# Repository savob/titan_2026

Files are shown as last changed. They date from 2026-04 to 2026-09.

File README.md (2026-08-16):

# TITAN Video System 2026

_One more swing!_

This is the code and hardware that is used to drive the electronics aboard TITAN for the "drive-by-video" system to be hopefully used for the World Human Powered Speed Challenge 2026. **This is heavily based on - and should really be considered a revision of the previous version I made in [2022](https://savobajic.ca/projects/extracurricular/titan-2022/).**

This code is spread across two types of devices, an STM32 microcontroller and Raspberry Pis (RPi) Model 3's. Each rider has an RPi for a total of two units, while there is only one STM32 needed for the vehicle. The STM32 is primarily responsible for collecting vehicle data and passing it to the RPis when requested while the RPis are responsible for displaying the video feed from the RPi Cameras used (hence why each rider needs their own) with an overlay of data collected inside the vehicle. This overlay is tailored to each rider.

There is an additional redundant video system for the front rider based on analog video to minimize potential failure points. This system was entirely off the shelf except for the power regulator, and was entirely disconnected from the remainder of TITAN's electronics to prevent any failure cascade affecting it.

## Folders

The repository is split into folders based on function.

| Folder | Purpose |
| --- | --- |
| `documentation` | Collected MarkDown files detailing various parts of operating TITAN. _NOTE: These are not exhaustive, check the various subsystem `README.md` files for information too!_ |
| `firmware` | Code for the embedded systems, namely the RPi HAT |
| `hardware` | Hardware files for our circuit boards |
| `vision` | Code used to operate the video system on the RPi |

## Hardware

The hardware for TITAN was all designed in [KiCad](https://www.kicad.org/) there are a few boards designed for TITAN with a `readme.md` explaining their purposes. Below is a block diagram of the TITAN system.

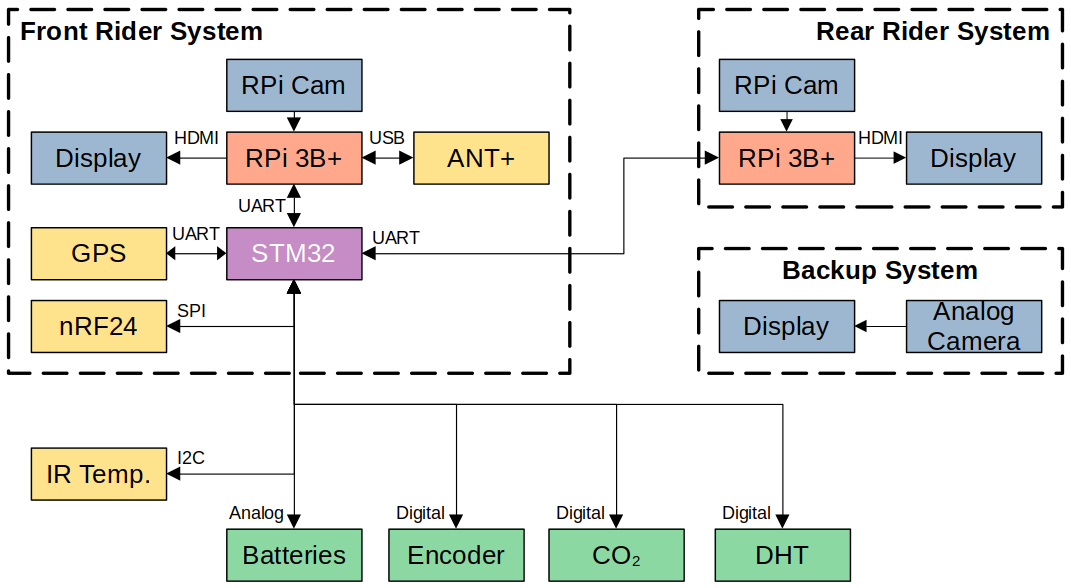
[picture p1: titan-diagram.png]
TITAN Block Diagram


## Microcontroller Code

This is the code prepared for the microcontroller on TITAN. It contains the overall program for TITAN, as well as potentially some other unit tests or variants.

## Raspberry Pi Code

These are responsible for putting video feeds from the outside on the displays for the riders to see from inside. These are overlaid with information collected about TITAN. One of the RPi's has an ANT+ USB module used to collect data from the heart rate monitor and power pedals each rider has and feed it to the STM32 to pass onto the rest of the system.

**The program for running the video feed is run as a separate process to the overlay**, this way if there is a hardware malfunction for the overlay (e.g. the STM32 freezes) then the video feed is uninterrupted for the riders.

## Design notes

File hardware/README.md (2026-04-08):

# TITAN Hardware

These folders contain the projects related to hardware designed to operate TITAN.

They were all designed using KiCad 10.0.

## TITAN Board

The main TITAN hardware is designed to be a HAT (**HA**rdware on **T**op) for the Raspberry Pi 3s we use for video feeds. These HATs perform power regulation for their video systems, data collection, and orchestrate communications between the different systems both inside and outside of TITAN.

## Wheel Board

In TITAN there is small board designed to be located near the wheel brake disks to monitor wheel speed and brake disk temperature for the main board to monitor.

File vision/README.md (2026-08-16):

# Vision Code

This folder is the collection of vision system code running on the RPis. Split between C and Python code.

>[!NOTE]
> Although these files can be viewed and edited off RPis they will only really compile and work properly on RPi 3 microcomputers due to the dependence on some hardware specific libraries, especially for the overlay functionality.

## Setup

>[!IMPORTANT]
> There is a bit of setup needed for this code to work assuming the system is not derived from an image of TITAN in 2022. However I am hazy on the details so this is my best guess.

To setup the ANT receiving system please follow the instruction in [HPVDT's fork](https://github.com/hpvdt/openant) of another fork of OpenAnt.

To configure the C build system for the overlay system one will likely need to execute the following shell commands, although I am unfortunately not certain if they're what I did all those years ago.

```bash
sudo apt install cmake
sudo apt-get install libraspberrypi0
sudo ldconfig -n /opt/vc/lib
```

## Operation

The RPis are configured to boot this system automatically when powered by executing the `titan_startup.py` script when booted (done by editing [rc.local](https://linuxhint.com/use-etc-rc-local-boot/)). To speed this process up, the RPis are configured to boot to command line (CLI) rather than starting the graphical user interface; we believe this also slightly improves the speed of the system.

`titan_startup.py` then launches a series of other processes that collectively represent the TITAN vision system.

- `power_button.py` watches for presses of the 'PWR' button
  - If tapped briefly it merely stops the vision system (useful for development). Entering `startx` into terminal is then needed to start the desktop environment.
  - If held for a few seconds it will shut down the RPi. Presing the button again will start the RPi.
- `camera.py` starts the camera feed and camera recordings

Once these are running, the startup script then responsible for determining whether the RPi is supposed to be the front or rear rider's system based on the presence or absence (respectively) of an ANT+ receiver, and launching the overlay program, `bike.bin`, accordingly by passing it the right arguments.

- If it is the rear system (no ANT+ modules connected), then the startup script just launches `bike.bin` with the arguments needed for the rear system.
- If it is the front system (ANT+ module present), then the startup script launches the `titanant.py` script to read the ANT+ data and pipe it into `bike.bin` to be overlaid and fed to the STM32.

**NOTE: All these scripts/executables are run as separate processes so that if one fails, the others should continue unhindered. Namely the video is never interrupted to the riders.**

## Overlay Code

The overlay code is the main product of this folder, and written in C. It is split up across several function specific C files. Handles communication with the STM32 for data, overlay drawing, and logging as requested.

- `main` - Main file. Reads in arguments provided to determine behaviour (e.g. 'front' or 'rear' system, record logs or not) and then run the main loop to create overlays.
- `antInterface` - Used to process the piped in ANT data from `titanant.py` for use on the overlays and passing on the the STM32
- `overlay` - Responsible for the actually drawing of the overlay. Uses the chipset driver library unique to the RPi 3 hardware to draw the overlay over the video feed. This limits its use to only the 3B or 3B+, and `bike.bin` must be compiled specifically for each model.
- `logging` - Used to write a CSV file of all data collected on the bike
- `racesim` - A C version of our Race Simulation file used to determine how our bike should perform and then compare to how it actually is to see if we're exceeding expectations or not. **UNTESTED**.
- `serialComs` - Responsible for handling communication with the STM32
- `timeTrial` - Used to monitor timing of the code to see how long different sections take to execute. *Used for development purposes, not needed for the riders.*

The code can be edited on the RPi itself, and this is fine for any small tweaks such as some hardcoded constants like wheel radius. However for any larger changes it will likely be easier to offload the editing onto a more capable computer to then copy the changed source code onto an RPi. The exact method to do this is up to you, but I generally opted to move the SD card between the RPi and my laptop.

### Compiling the Overlay Code

If changes are made to any of the Python files, ending in `.py` then one only needs to save and close the files once satisified with the edits made for them to take effect on the next run.

With any changes to the overlay source code in C in the `.c` or `.h` files, one will need to compile a new `bike.bin` for them to take effect.

>[!IMPORTANT]
> Regardless of how the code is edited, it **MUST be compiled on an RPi 3 itself**. This is because overlay code makes use of low level video drivers (VideoCore) for the Broadcom chip that runs the RPi 3 computers, as well as some specific features for some timing code. It is for this reason that many of the `#include` statements and constants will likely be flagged as errors on a non-RPi computer.

The compilation process is based on using a `Makefile` so to generate a new `bike.bin` simply execute the following command in this folder.

```bash
# If changes were only made to .c files
make

# If changes were made to any .h files a clean will ensure they're properly recompiled with .c files
make clean; make
```

The full procedure for this is roughly:

- Replace the contents of the `/home/pi/Desktop/vision` on the RPi SD card with the new file(s)
- Reseat the SD card in the RPi and boot it
- If the video system starts, tap the power button on the RPi HAT to kill the video system and reveal the terminal
- Navigate to the vision folder with `cd /home/pi/Desktop/vision`
- Run `make` in that folder to compile the new binary
- Reboot the system if no errors occur

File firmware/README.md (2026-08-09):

# Microcontroller Code

This folder contains the firmware projects for the embedded system within TITAN going into competition for 2026, targeting the STM32 microcontroller on board. The base for these is the original project from 2022, which was written using the Arduino IDE within the PlatformIO system. Unfortunately I didn't check it before upgrading the microcontroller but the STM32F105 series **lacks any compatibility with the Arduino framework** so a direct port is impossible at present.

This has forced my hand into remaking the project using STM32CubeIDE which is now complete. All code going into the embedded system will be written in C with potentially some C++.

>[!IMPORTANT]
> These firmware projects will generally have "Debug" and "Release" build/upload options. Whenever programming a board to be used in the field **ALWAYS select the "Release" version** as they will be more optimized by the compiler and have some debugging systems (e.g. testing `printf()` lines) stripped out in the pursuit of performance. Only use "Debug" when actively working on a development or performance is not important.

| Project | Purpose |
| --- | --- |
| `titan_2026_rev_a` | Principle firmware to run TITAN boards during races (for both primary and secondary boards) |

## Programming the Boards

To program the STM32 based boards, some version of an STLink is needed to form the connection via a ribbon cable. The [STLINK-V3MINIE](https://www.st.com/en/development-tools/stlink-v3minie.html) is a good tool for this and can be had for a reasonable price. There should be a few of these around the workshop.

>[!TIP]
> The MINIE will not supply power so connect a battery or USB cable to targetted systems. When connecting the ribbon cable to the RPi HAT boards (Rev. A) then the cable is connected such that it covers the LEDs.

If the MINIE is not available there are other more expensive variants or even STM32 development boards also have these built in and can be easily repurposed to program other boards.

>[!NOTE]
> In the past we used bootleg STLink V2 programmers but these will not be recognized and used by STM's software. These also lack consistent pinouts and the protections offered in official offerings.

With the programmer connected to the target board you will then be able to upload firmware using the [STM32CubeIDE](https://www.st.com/en/development-tools/stm32cubeide.html) (compiling from source code) or the [STM32CubeProgrammer](https://www.st.com/en/development-tools/stm32cubeprog.html) (if you have precompiled binaries). For more details on the uploading process refer to ST's own documentation depending on the software used.

## Software Used

All firmware was written using the [STM32CubeIDE](https://www.st.com/en/development-tools/stm32cubeide.html), the projects were configured using [STM32CubeMX](https://www.st.com/en/development-tools/stm32-configurators-and-code-generators.html). These, and most of ST's software is all crossplatform and free to use.

Of these two, STM32CubeIDE is needed to tweak, compile, and then upload firmware. MX is less likely to be needed since that is only used to initally configure the projects and generate code for their hardware, e.g. setting pin functions or configuring communication buses. These configurations don't change significantly except with hardware revisions.

As mentioned earlier the [STM32CubeProgrammer](https://www.st.com/en/development-tools/stm32cubeprog.html) can be used to flash microcontrollers and perform some basic debugging. The problem is that is can only really upload pre-compiled firmware files so you cannot change the firmware using it, for example to adjust wheel diameter.

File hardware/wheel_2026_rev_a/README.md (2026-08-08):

# TITAN Wheel 2026 Rev. A

This board houses a brake temperature sensor as well as a wheel encoder for monitoring speed and distance. It was designed to fit within the wheel bracket close to the brake disk without interfering with the rider's pedaling.

## Changes from 2022

The main changes from the last version will be in improving physical reliability of the system

- Changed everything to other than sensors to be surface mount on the top of the PCB to eliminate the possibility of shorting against mounting surface
- Changed operational amplifier to a TLV2372IDR instead of an LM358 for better performance, namely rail-to-rail output
- Using pads to connect the data cables, headers can be soldered in later if desired
- Removed connector to daisy-chain wheels since that is now handled on the HAT
- Added notes to operate at 3.3&nbsp;V not 5&nbsp;V - although the system can handle it

Looking on data from 2022, there was some noise on the encoder speed signal when plotted alongside the GPS derived speed. This could potentially benefit from filtering the signals, although I would really chalk it up to my firmware not properly capturing each spoke and not using a hardware timer.

## Tuning the Encoder's Comparator Operation

The onboard comparator circuit for the wheel encoder needs to have the two potentiometers to be properly set for reliable operation. One is responsible for the baseline threshold the encoder is compared to to know if the spoke is present of not, labeled `THRES`. The other potentiometer adjusts the level of hysteresis preventing spurious switching by moving the active threshold so the signal can't repeatedly cross it, labeled `HYST`.

To begin, the board must be installed into the wheel bracket and powered, _ideally via the TITAN HAT_. An oscilloscope is strongly recommended to probe the test pads while doing this to complete it accurately but, but not necessary. If possible, perform this with the wheel enclosed in its fairing - or out at least out of direct sunlight as it may influence the IR sensor.

### Without an Oscilloscope

1. Connect the target wheel board to an RPi HAT board and supply power to the HAT board to power the sensor board - battery or USB power is fine.
2. _Gently_ turn both potentiometers entirely counterclockwise to reset them.
3. Rotate the wheel so that the IR sensor is entirely clear of any brake disk spokes.
4. Check that the LED is lit up, if not there may be an issue with the board or too much ambient IR which will need different conditions for testing.
5. Rotate the wheel so a spoke is directly in front of the IR sensor.
6. Turn `THRES` clockwise to increase it until the LED turns off, remember this as the "low" mark.
7. Spin the wheel and make sure that the LED is turning off with each passing of a spoke, and then back on again. Gradually increase `THRES` by turning it clockwise until the LED is no longer turning on again when the spoke is gone - this is the "high" mark.
8. Set `THRES` to be halfway between the "low" and "high" mark. Spinning the wheel should have the LED flash again with each spoke pass.
9. Keep spinning the wheel and increasing `HYST` by turning it clockwise.
10. Once the LED is no longer changing state with the wheel's rotation, this it the "high" mark.
11. Set `HYST` to be about halfway from the starting/zero point to the "high" mark.
12. Spin the wheel to ensure that the LED is flashing again.

This should roughly center the threshold correctly and provide a decent level of hysteresis. _It is impossible for the human eye to perceive the true effect of hysteresis with the LED alone, so we're basically just guessing this._

### With an Oscilloscope

The precise way to do this, no _major_ guesstimations here!

1. Connect the target wheel board to an RPi HAT board and supply power to the HAT board to power the sensor board - battery or USB power is fine.
2. _Gently_ turn both potentiometers entirely counterclockwise to "reset" them.
3. Rotate the wheel so that the IR sensor is entirely clear of any brake disk spokes.
4. Check that the LED is lit up, if not there may be an issue with the board or too much ambient IR which will need different conditions for testing.
5. Read the voltage on the test point labeled `RAW`, this is our ambient level.
6. Rotate the wheel so that there is a spoke directly in front of the IR sensor.
7. Record the voltage on the test point labeled `RAW`, this is our presence level.
8. Gradually turn `THRES` potentiometer until the voltage on the test point labeled `THR` is halfway between the ambient and presence levels. _If the spoke is still in front of the IR sensor at this point, the LED should turn off._
9. Spin the wheel to observe the LED turning on and off as the spoke passes.
10. Keep the wheel spinning and probe `OUT`.
11. Gradually increase `HYST` by turning the potentiometer clockwise until the signal on `OUT` shows a single pulse for each spoke pass rather than a series of pulses during the transition. Then turn `HYST` a sliver more - just not too much so that the `OUT` stops switching
    - If you're also able to probe the other two signals you should be able to see that `THR` is changing between two levels and that `RAW` should be able to cross `THR` only once per spoke passing.
    - `RAW` should continue to a level past `THR` after crossing it, so that even if `THR` didn't move `RAW` would not be causing potential switching with any sensor noise.
    - If the hysteresis gets too large then it might make it hard to catch occasional pulses leading to slower perceived speed.
12. Spin the wheel to ensure that the LED is flashing with each spoke passing.

## Known IR Encoder Issue

There is a fundamental issue with the use of the IR sensor for the wheel encoder: the wheel encoder would fail to track the wheel speed once the brakes were engaged as it gets saturated due to IR radiation from the brake disks reaching temperatures in the multi-hundred degrees as they stop TITAN at the end of runs.

This issue was tolerable as we still had the GPS speed to fallback to, and the brakes would only be engaged when a run was ending so there was no longer a need to know TITAN's exact speed. **Future revisions should consider a different sensor type for the encoder, but this revision kept it since it was field proven and doesn't require modifications to TITAN's wheels.**

A possible hack that could be done using these boards as-is, would be to replace the IR sensor with a visible light discrete LED and photodiode or photoreceptor pair. This should avoid the issue where the brake disk temperature affects the sensor while retaining compatability with the wheels as they are.

A larger overhaul of the board could move to using a magnetic system by attaching magnets to the spokes. If wheel modification is to be avoided, then inductive or capacitive proximity sensing system for the spokes could be considered but the rework needed there would be significant and need collaboration with the mechanical team.

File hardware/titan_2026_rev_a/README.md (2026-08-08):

# TITAN Board

The main custom board for TITAN is designed to be a HAT (**HA**rdware on **T**op) for the Raspberry Pi 3s we use for video feeds. This baseform form factor was inherited from the 2022 version. At the heart of the HAT, there is an STM32 microcontroller which communicates with the RPis and various sensors around TITAN via the various connections present.

## Functionality

These HATs perform four main functions:

1. Regulate power for their RPi and monitor from the battery
2. Facilitate communication between RPis via an STM32 microcontroller
3. Collect data from TITAN using the STM32 microcontroller
4. Handle telemetry broadcast out of TITAN

**Functions 2 to 4 only need to be performed on the "primary" (front rider's) unit.** The secondary (rear rider's) only needs to merely power the RPi and display, and connect to the primary board.

### Power Regulation

These boards receive power directly from LiFePO4 batteries which needs to be regulated down to 5&nbsp;V for the RPi to use, and passed to the display.

The main 3.3&nbsp;V rail for logic will be taken from the RPi for board logic. However there will be an linear regulator and power switch to allow for the USB to power the board safely in the absence of an RPi.

Historically we used 3S packs with a nominal voltage of 9.9&nbsp;V which when really discharged would lead to some screens dimming their backlights, although never fully turning off. So for 2026 I am considering going up to 4S to prevent this happening.

### Sensors

The board hosts several sensors to monitor different things around TITAN. Some sensors are located off board to be better positioned to capture their data such as the wheel sensors. A summary of the sensors interfaced directly with the STM32 in the system is:

- Encoder based wheel speed and distance traveled
- GPS based speed/distance
- Battery levels
- CO2 levels
- Brake temperatures
- Ambient temperature and humidity

### Communication

The STM32 acts a server essentially for data, serving and accepting data from the different system endpoints. Communication with the two RPis is done via UART, and out of TITAN using nRF24 radios.

### Configuration

All boards will be assembled identically, so setting a board for operation in a "primary" or "secondary" role will be needed.

This is partly achieved through hardware design with the `ROLE` signal, but some solder jumpers are needed to portion off the I2C bus on the secondary board to avoid address collisions when connected.

Depending on the displays used there is a solder jumper to provide them with power from either the 5&nbsp;V rail or directly from the battery.

Furthermore there is an additional solder jumper to set the voltage supplied to the wheel sensor system. In 2022 they worked at 5&nbsp;V, but checking the sensors over they should have been supplied 3.3&nbsp;V - so I put the jumper to easily use one or the other.

### Standalone Operation

Although not an critical design constraint, I would like these boards to be able to operate on their own for testing and even use as downlink boards for the crew outside TITAN. So I have incorporated a USB-C connection and some power switches to safely connect to the USB under any configuration of the board.

## Changes from 2022

There are a multitude changes between the 2022 and 2026 versions of the TITAN board, however my desire is to make them all transparent to the system at large (RPis), and minimize the complexity of firmware rewrites for the STM32. In approximate order of implementation:

- Added isolators to be used for inter board UART lines
- Integrated a GPS module
- Integrated environmental sensors
- Using proper wire to board connectors for everything rather than expecting to soldering some wires to the PCB
- Added sensor to monitor battery voltage and current draw per board
- Changed the main microcontroller to an STM32 with more GPIO (STM32F105R)
- Removed reverse polarity input protection for simplicity
- Removed input undervoltage protection, to accommodate varying batteries
- Added on board regulator and power switch ICs to run off USB power if not mounted on an RPi ("standalone")
- Board "role" is determined in hardware based on the connection between the primary and secondary
- Added jumper to select power output to the display connector
- Introduced solder jumper to set wheel power level after finding the sensors used in 2022 were actually rated for 3.3&nbsp;V, _not 5&nbsp;V!_

These cover all the changes I felt were really needed on TITAN. There was only one change that I would like but couldn't justify: integrating the nRF24L01+LNA radio used for telemetry. It would needlessly take me more time to draw the schematic, spec the parts, and then layout while not meaningfully improving any performance metric while greatly increasing the cost compared to just getting a handful of the preassembled modules online. _I'll put aside the vain desire for a majestic monolithic PCB, for now._

## GPS Antenna Network Failure

There is only one critical issue with this board and that's the GPS antenna network routing. This causes the on board GPS module always reports "ANTENNA OPEN" even with an antenna connected or a short to GND. **To work around this issues, an off board module with a separate antenna connection should be soldered in place of the onboard one and use its RX/TX lines.**

Should another revision be made the following steps should be taken to hopefully address this:

- Add via stitching for GPS signal line from antenna to module
- Remove sharp routing bends
- Do not break return path (GND) underneith the GPS signal line
- Move the GPS module more north on the PCB to afford more space for nicer routing
- Choose trace width for a 50&nbsp;Ohm impedance in the final stackup used
- Change components on antenna line to match exactly with known good ones:
  - 6.8&nbsp;nH inductor: Murata LQG15HS6N8J02D
  - 470&nbsp;pH capactior: FH 0402CG471J500NT
  - Connector _(optional, but best to avoid discrepancies)_: BAT Wireless BWU.FL-IPEX1

Below is a figure of the known good reference layout used in another design.

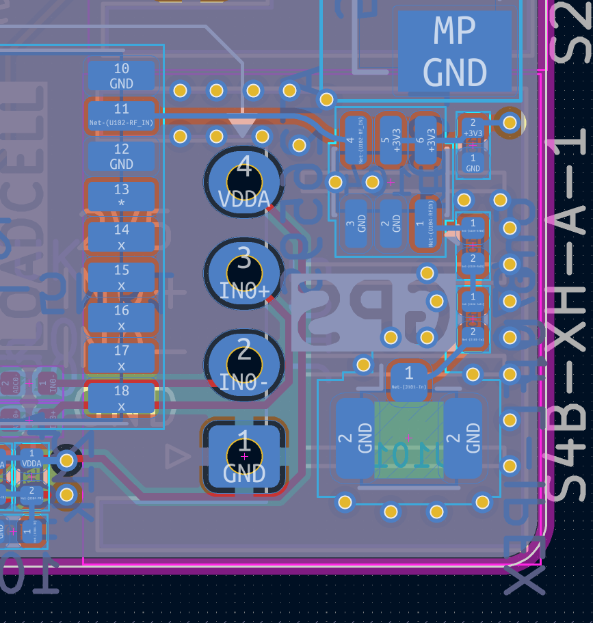
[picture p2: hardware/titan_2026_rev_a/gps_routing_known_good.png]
Known good GPS layout for reference


_This is the first time I've had such issues with radio work so I'm quite dissappointed in this outcome._

## Potential Improvements

These are some minor changes one should consider if a revision or derivative of this work is considered:

- Brake disk temperature sensors work fine at 3.3&nbsp;V so we can remove that solder selection jumper
- Change the serial peripheral facing the secondary system from a UART to a USART so it can make use of DMA receives and transmits
- Add a solder jumper to connect the STM32 to RPi RX so we can ensure that the STM32 secondary board MCU doesn't contest the signal coming from the primary board
- Integrate nRF24 radio circuitry onto PCB
- Change the board so the INA219 is always connected to the STM32 on board, with some knockon changes:
  - No need for the solder jumpers on that I2C line
  - This removes the need for an I2C isolator system, simplifying the isolation requirements
  - The STM32 will always need to be active so the RPi serial line will connect via it to the other board
  - Secondary STM32 will need to poll the INA219 regularly and share that with the primary system

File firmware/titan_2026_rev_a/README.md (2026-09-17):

# TITAN 2026 Code

This is the code meant to operate the entire system. It is meant to be flashed onto bothe boards present in the bike, regardless of position, they will determine their role based on the connections made to them on boot and act appropriately for their role. This firmware was written to provide a transparent replacement for the original 2022 system, so the vision systems can interact with it just like they did with the previous board.

>[!NOTE]
> Although this was meant to facilitate a transparent replacement of the old TITAN electronics system, there are some changes which do slighly break compatibility with the old vision system outlined in the [section on changes](#differences-from-titan-2022).

## Status LEDs

There are three status LEDs located centrally on the board used for various purposes. They are labelled `STATx`, `STAT1` is red while `STAT2` and `STAT3` are white. All these LEDs can be dimmed. Below is a table summarizing various status LED states. If "X" is used then that light doesn't matter to communicate something - for example with non-critical errors. When an LED is "cycling" it is gradually brightening up to a point where it turns off and restarts; the brightness effectively following a sawtooth pattern.

| `STAT1` (Red) | `STAT2` (White) | `STAT3` (White) | Meaning |
| :---: | :---: | :---: | :--- |
| Flashing Quickly | OFF | OFF | **Critical error encountered, microcontroller will reboot momentarily!** _Note: this will not interrupt the video systems._ |
| Cycling dimmly | X | X | **Non-critical issue encountered**, sensor system will continue to fulfil its role in a dimished state. _A sensor might be disconnected._ |
| OFF | X | X | **No issues detected** in by this board as this role. |
| X | OFF | ON | Board is operating as the **secondary board**. |
| X | Cycling | ON | Board is operating as the **primary system, GPS lock in progress.** |
| X | ON | ON | Board is operating as the **primary system, GPS lock completed.** |

## Primary Role (Front Rider)

If determined to be on the primary video system board, the microcontroller will assume the task of operating all real-time tasks for TITAN. Collecting all the data from around the bike's various sensors, processing the data into usable formats, handling communication between the microcomputers running the video systems, and even broadcasting data over radio.

When starting up it will check for all the sensors it expects in the system, should any fail to be identified or configure themselves the microcontroller will ignore them and continue operation. Recovery after boot is not a behaviour yet, so if a sensor is reconnected during operation the system will not notice until rebooted.

>[!IMPORTANT]
> The primary board uses a watchdog timer to ensure it does not get frozen and as a recovery mechanism after a critical error. This means that if the microcontroller freezes or otherwise fails to reset the watchdog timer before it hits zero, the microcontroller will reboot and try to recover with a clean(er) slate. The system has been configured that if such a watchdog reboot occurs then the vehicle data will be preserved into the next boot preventing the loss of distance covered and other measurements. This reboot will not interrupt the video systems in any meaningful way other than a temporary break in data updates.

## Secondary Role (Rear Rider)

When the microcontroller determines it is serving on the secondary system is simply illuminates the status LEDs to indicate this and enters an infinite loop of idling so it doesn't interfere with the operation of the system. No information is collected by or passed through the microcontroller in this role.

## Differences from TITAN 2022

There is **one breaking change** from 2022 which will cause unexpected behaviour on the vision system: instead of reporting the encoder-based (wheel) distance in rotations to the vision system _(which then multiplied it by the wheel circumference itself)_, that distance is now expressed directly as metres to the vision system. This removes the need to maintain the wheel circumference on the vision systems in addition to the microcontroller. The vision code in this repository is compatible with this new method.

Another, minor but not breaking difference is from before is that **we are completely ignoring the DHT11 sensor** as it is very slow to update and requires a long blocking read which would ruin the general responsiveness of TITAN. In its place there is an on board [BME280](https://www.bosch-sensortec.com/en/products/environmental-sensors/humidity-sensors-bme280) sensor to provide the same data in a much faster way, the only downside is that by being mounted on the board it will not be able to accurately measure the outside environment and it'll likely deal with self-heating from the RPi underneath it.

## Potential Improvements

The code as is, can function as a drop in replacement for the 2022 boards (with modified connectors). There are a few minor features or improvemetns that are being considered for future firmware versions:

- [ ] Autodetect the SCD-4x variant used on the board, and add altitude adjustment
- [ ] Add system to adjust the readings from BME280 to approximate the exterior if desired
- [ ] Have the secondary board firmware check if it can find the INA219 IC on the bus to alert users to inproper configuration somehow
- [ ] Make use of the USB connection perhaps for additional debugging interface

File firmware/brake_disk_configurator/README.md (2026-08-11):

# Brake Disk Sensor Configuration Utility

This firmware was made to allow TITAN's brake disk sensors to be configured and tested prior to operation. It is operated using the UART connection via the debug connector, since you'll need that to flash the MCU anyways. Using the debugger will also safely preserve your connection to the system as you potentially power cycle TITAN.

>[!CAUTION]
> Always make connections when the system is unpowered! Please avoid "hot-plugging" the sensors into a powered TITAN board, this may cause damage to the electrical hardware.

## How to Use the Configuration Software

Once you have the firmware flashed to a TITAN 2026 Rev. A board and with the debugger still connected, open a serial terminal on your computer and connect to the debugger's serial port at a **Baudrate of 115200**. Then enter commands as desired, _no need for any newlines or such_. The board processes commands once every couple of seconds so please be patient! All commands follow format `CAA,P` where:

- `C` is the command character
- `AA` is the target senor's I2C address in hexadecimal, e.g. `5A` instead of `90`, _if appicable_
- `P` is an optional parameter _(if not needed for a command the leading comma may be ommited)_

>[!TIP]
> Occaionally only the command character is captured from the user's input, if this happens simply repeat the message until properly received - no harm will come from this. There is no user input that can cause damage to the system.

| Command character | Operation | Address Needed | Parameter |
| :---: | --- | --- | --- |
| `H` | Print help message _(a basic summary of this table)_ | No | None |
| `S` | Scan the bus and report any responsive addresses | No | None |
| `O` | Read object temperature from the sensor | Yes | None |
| `A` | Read ambient (sensor's own) temperature from the sensor | Yes | None |
| `E` | Set object's emissivity as P | Yes | Decimal digits of emissivity (as many digits as desired), e.g. `E5A,769` to set emmisivity of 0.769 at `0x5A`, use 0 to set 1.000 |
| `C` | Change sensor address | Yes | New address in hexadecimal |

>[!NOTE]
> Changes to address and emmissivity properly take effect after the sensor is power cycled.

## General Procedure

If I were doing this I would follow this procedure roughly, the important thing is to ensure that we have sensors at the right addresses above all else so they don't have address collisions inside TITAN since all **sensors are shipped with a default address of 0x5A**. Emmisivity and temperature tests can follow later.

1. With TITAN powered off connect the front brake disk temperature sensor to the bus using the right connector
2. Power up TITAN and run a scan using the appropriate command, only one address should be listed, likely `0x5A`
3. Change this address to the desired address (likely `0x01`, check with a firmware nerd) for the front sensor using the appropriate command
4. Power cycle the system
5. Perform a scan to confirm the address change took effect
6. Power down the board and disconnect the front sensor
7. Repeat steps 1 through 6 with the rear wheel sensor instead, to set it to an address of `0x02` (double check with the firmware nerd)
8. With TITAN powered down connect both sensor
9. Power up the system and conduct a scan and check that both sensors are reporting at their appropriate addresses
10. _(Optional, but recommended)_ Adjust the emissivity of both sensors to match the brake disk material, in 2022 we used `0.600`.

With this done, the rest is really just playing around checking it is reading appropriate temperatures when objects are infront of a given sensor.

>[!IMPORTANT]
> In summary the following parameters should be set before TITAN goes out for a run.
>
> - Front wheel address should be `0x01`
> - Rear wheel address should be `0x02`
> - Both wheels should have an emissivity of `0.600`

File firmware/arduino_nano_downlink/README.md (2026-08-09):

# Arduino Nano Downlink

A simple serial to nRF24 bridge for receiving TITAN braodcasts onto a host PC. Potentially even sending data back to TITAN using acknoledgement packets.

This firmware exists primarily to aid in the development of the radio broadcasts of TITAN by using a known good library. The target hardware is the super old telemetry boards I made to have an nRF24 module backpack on an Arduino Nano, which used the default pinout for the library at the center of this, [RF24](https://github.com/nRF24/RF24).

_The baseline code was taken from the firmware unit tests for TITAN 2022._

## Hardware preparation

This project is prepared for an Arduino Nano with the original bootloader, although it can be easily reconfigured to work for a Nano with the new bootloader or even the classic Uno using the same pinout.

The connections needed to be made are as follow. They are listed in order from pin 1 on the nRF24 (indicated with the square pad) to its neighbour (pin 2) before advancing to the next row.

| Arduino | nRF24 |
| ---: | :--- |
| GND | GND |
| 3.3V | VCC |
| 7 | CE |
| 8 | CSN |
| 13 | SCK |
| 11 | MOSI |
| 12 | MISO |
| 2 | IRQ |

>[!NOTE]
> On the Arduino Nano pin 13 (SCK) is used for the built in LED so it cannot be used in this code, and will flash when there is any SPI activity between the Arduino and radio.

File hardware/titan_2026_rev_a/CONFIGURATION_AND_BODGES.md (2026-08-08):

# Configuring and Fixing TITAN 2026 Rev. A Boards

Before use these board will need the attention of a soldering iron to prepare them for proper operation. It is assumed that you will have access to a soldering iron, a hot air rework station, solder _(preferably lead-free)_, solder flux, solder wick, and tweazers.

## Bill of Materials

The boards weren't fully assembled by the vendor so far, so the following parts are needed to complete the board and complete any fixes. _These numbers are all per board._

- 1 unit - 40-pin (2 rows x 20) 0.1" female pin header, to connect to the RPi.
- 4 sets - 2.5M spacers to hold the HAT to the RPi.
  - Preferably plastic to avoid shorts or damaging the boards.
  - A perfect fit would need 11&nbsp;mm tall spacers but those are rare, so the more common 10&nbsp;mm can be used instead without issue.

These parts are optional, depending on if certain fixes or "upgrades" are desired.

- 1 unit - SCD-41 CO2 sensor. _The SCD-40 can be used too if necessary._
- 1 unit - Replacement UART 3.3&nbsp;V GPS module. The "Ultimate GPS" from 2022 can be used or most other GPS modules readily found online. _Ideally find one with an SMA connector but adaptors exist._
- 1 unit - nRF24L01+LNA module with an SMA connector, to enable telemetry. There should plenty at the workshop, otherwise they're readily available and pretty standardized online.

## Completing the Board

Although the boards were largely assembled by a third party, some pieces were ommitted for various reasons _($$$)_ and need to be hand installed on **ALL** the boards. These parts should be installed in the order below.

1. Solder the 40-pin header for the RPi to the bottom of the board so the HAT may be seated atop the RPi.
2. Proceed to [complete the solder configurations](#configuration-via-solder-jumpers) needed
3. Complete any desired bodges/upgrades listed below
4. Once all soldering is completed to a board, use the spacers to firmly mount the HAT to the RPi before installation into TITAN.

## Configuration via Solder Jumpers

On the TITAN board there are a three clusters of solder jumpers that need to be properly set for the boards to work.

>[!NOTE]
> No damage will occur if any jumper is left open, but it will likely lead to degraded performance since most of these route power or data around the system needed for things to work properly.

### Wheel Power Selection

The first one in the north west, by the power button is for setting the power supply to the wheel boards. **Bridge this one so that `3` is connected to the middle on ALL boards.** This was for development to see if the wheels can reliably operate at 3.3&nbsp;V or if 5&nbsp;V was needed. _If this is incorrectly connected to `5` instead the system will still work, but some damage may happen to the brake temperature sensors with prolonged operation._

### Board Role Selection

Moving toward the microcontroller there are two jumpers that need to be set together to put the board into a primary or secondary role. If the board is meant to function as a primary board connect the pads by `PRIM` to the center, otherwise connect the ones by `SEC`. This will direct to which microcontroller the onboard power monitor connects to so the battery level can be monitored. Connecting the two center pads to different ends will not cause catastrophic failures, however bridging `PRIM` to `SEC` through the middle will cause TITAN systems to fail.

### Monitor Power Selection

The final _mandatory_ bridge is between the two XT-30 connectors. This selects what voltage to apply to the monitor XT-30 between the battery voltage or the onboard regulated 5&nbsp;V rail. Solder this based on the selection of battery and monitor. _I would suggest to use the battery voltage if possible, otherwise the RPi and monitor will fight for the 15&nbsp;W available from the regulator._

### Inter Board Ground Connection

Lastly there is a bridge labelled `GND TIE` near the inter board connectors, **this one can be left open with no drawbacks**. It connects the GND of the two baords together that would otherwise be totally isolated - which enables electrical probing across the two boards, but does slightly undermine some of the protection that the isolation chip offers. _This bridge has no effect on secondary boards._

>[!IMPORTANT]
> Since probing from one board to another is unlikely to ever be needed _(I personally never needed it during my testing of TITAN)_  I strongly recommend that the ground tie (`GND TIE`) be left open for any racing TITAN hardware to offer the maximum protation to failures.

The image below shows a completed TITAN board with the solder jumpers configured for primary operation, with battery power supplied directly to the monitor, and its ground connected to the secondary. _Please ignore the damage to the battery XT-30 from careless soldering!_

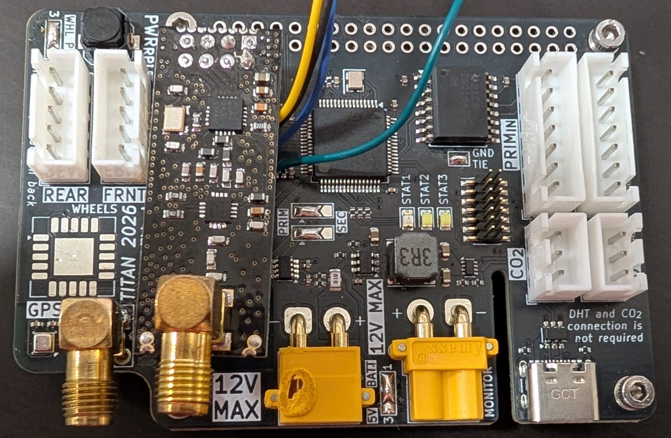
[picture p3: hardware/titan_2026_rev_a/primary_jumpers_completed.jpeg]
TITAN PCB configured for primary operation with the monitor powered directly from the brain


## GPS Issue and Replacement Fix

The only issue the Rev. A board carries is that the GPS antenna circuit doesn't work, rendering the onboard GPS module useless. Leaving the GPS module present will not negatively impact the system, it will simply not provide any useful GPS data to use.

The faulty GPS system can be replaced with a functional off board module with bit of work:

1. Remove the useless GPS module (module with a QR code sticker on top, near the GPS antenna). Be careful to not deform the plastic wheel connectors nearby.
2. Solder wires to the functional pads for the GPS module to connect the offboard module. **`GPS_TX` connects to the TX output of the GPS** module, `GPS_RX` to RX of the GPS.

The connections made to the GPS footprint are shown labelled below.

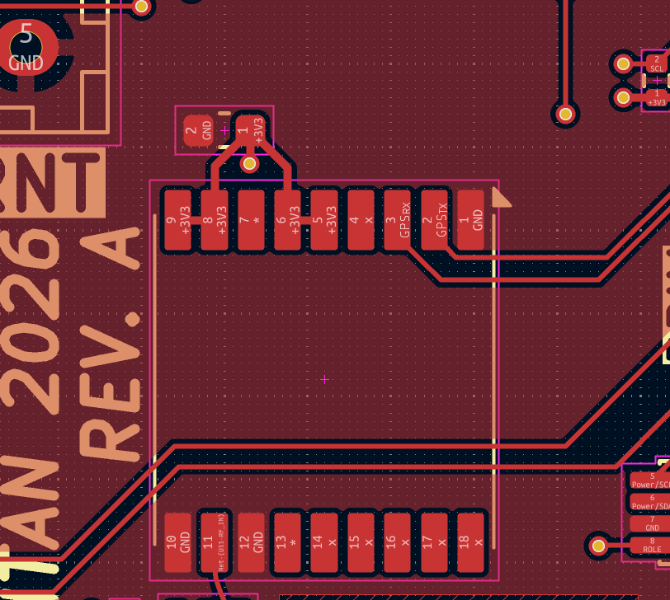
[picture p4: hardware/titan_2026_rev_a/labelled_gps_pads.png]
Labelled pads of the GPS footprint


The image below shows the final result with wires soldered on. Yellow wire for power, black for GPS RX, blue for GPS TX, and green for ground _(don't question the choice of colours!)_

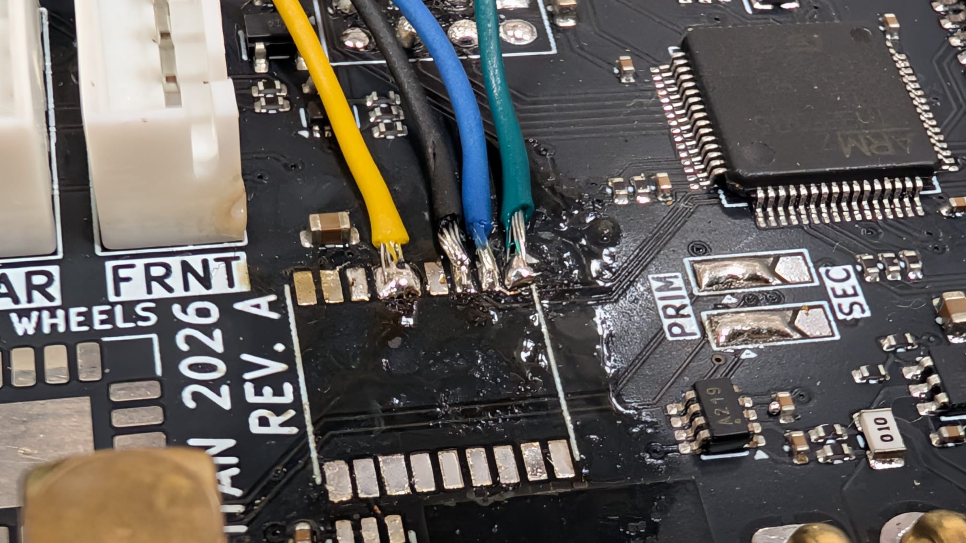
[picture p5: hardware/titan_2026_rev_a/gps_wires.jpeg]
GPS wires connected to vacated pads


## Upgrades, Upgrades

There are some optional things that can be done to improve or make full use of TITAN. TITAN's firmware is designed to check for these and adjust automatically so if these are absent then TITAN will continue to operate without issue.

>[!IMPORTANT]
> These upgrades will only be used if the board is acting as a primary, so there is no need to perform these on boards destined to serve as secondaries.

### SCD-4x CO2 Sensor

This is a low-power digital CO2 sensor that has a footprint allocated on the PCB by the GPS antenna but was ommited from assembly due to its cost and the fact that we already have a decent sensor with the MH-Z19B that covers the same range - albeit power hungry.

The SCD-41 should be used since it has a higher range (400&nbsp;to&nbsp;5000&nbsp;ppm), but the SCD-40 (only 400&nbsp;to&nbsp;2000&nbsp;ppm) is pin compatible in a pinch and the code will retrieve data all the same regardless. The SCD-40 is likely to be overwhelmed during a true run based on previous data showing conditions exceeding 2000&nbsp;ppm quickly into a run.

Placing it on the board is a standard SMT reflow operation. The decoupling capacitor it requires is already populated so only the sensor needs to be placed in the proper orientation.

### nRF24 Radio Installation

Soldering an nRF24L01 module to the empty footprint between the microcontroller and the power button for the RPi will allow the board to broadcast telemetry to a downlink in the chase vehicle or elsewhere. This is a simple through hole soldering operation, simply seat the radio so the antenna connector points the same way as the GPS antenna and solder it down.

>[!CAUTION]
> The nRF24 module will obstruct the GPS module region of the PCB, so do any work on the GPS system prior to installing an nRF24 radio module. This can be seen in the image of the completed solder jumpers.

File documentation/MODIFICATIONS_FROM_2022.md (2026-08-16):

# TITAN Modifications from 2022

There were some hardware changes from 2022 to 2026, these are all principally in the embedded "sensor" system which will need some changes to be made to the TITAN system. For a complete list of changes refer to the `README.md` files for the [main board](../hardware/titan_2026_rev_a/README.md#changes-from-2022) and [wheel board](../hardware/wheel_2026_rev_a/README.md#changes-from-2022) as this will summarize the ones that need to be acted on. These will be sorted into sections based on descending importance to complete.

>[!IMPORTANT]
> This does not cover the modifications and finally assembly needed for the boards themselves, refer to their configuration guides as needed. So far only the main board, the RPi HAT needs [additional hardware work](../hardware/titan_2026_rev_a/CONFIGURATION_AND_BODGES.md) before use.

## Bill of Materials

These are the materials needed to renovate the bike, excluding those to modify/fix anything on the new circuit boards which is covered in their respective guides.

- XT-30 cable connectors, at least 10 of both types
- JST-XH connector kit; with 3-, 5-, and 7-pin connector housings and crimps

## Mandatory Actions

These are actions that must be completed for the new hardware to be usable in TITAN, note that these will make it incompatible with earlier versions as a result.

- **Replace the HAT to HAT cable** this was a 4-pin cable but now will be a 7-pin JST-XH cable.
  - The cable should be a "crossover" cable, so pin 1 on one end goes to pin 7 on the other, and so on.
  - An easy check is if you plug both ends of the cable into the RPi HAT board, the connections should be adjacent to one another. What I mean is that the top connection on `PRIM_IN` should be the same as the top on `SEC_OUT`, and continuing for the length of the connector. If a ribbon cable is used, it should just fold over, but not need twisting to occupy both connectors.
- **Prepare the new 2026 RPi HAT boards** as per their [configuration guide](../hardware/titan_2026_rev_a/CONFIGURATION_AND_BODGES.md) and replace the 2022 HATs
- **Change the battery connectors** from barrel jacks to XT-30F for the RPis
- **Change the monitor power connectors** (to the HATs) from barrel jacks to XT-30M
- **Split the brake/wheel sensor cable harness Y** into a separate one for front and rear wheels
- **Crimp the front and rear wheel sensor cable to use a JST-XH** 5-pin connector abiding by the pinout on the PCB.
  - _Note: not all connections need to be used if not desired. E.g. the front wheel may not use the encoder._
- **Update the power scripts on the RPi** to reflect single button for on and off if using the SD card image from 2022.
  - These are found alongside the vision system code at `/home/pi/Desktop/vision/` on the `rootfs` partition of the SD card

## Optional Changes

These are changes that would be nice and improve TITAN in some way, but are not needed for the system to function.

- **Replace the brake disk sensor board from 2022 with the 2026 version.** The newer boards are almost identical electrically but should present far fewer chances for things to short out and be more reliable in the long run. Soldering the wires to pads can help ensure a low profile cable run preventing damage from riders.
- **Replace the USB-A intermediate wire-to-wire connections with locking connectors** to improve reliability against vibrations. The exact connector doesn't really matter as long as it has a locking feature. _This was a design choice made by me back in 2019 and has carried forth to today, I know much better now!_ If I am not mistaken this is only at the front fork.
- **Replace the four conductor cable used to connect the front wheel sensor with a five conductor one** so the front encoder can be used as well if the wheel board is installed there.
- **Get smaller batteries.** The ones we used in 2022 were 2200&nbsp;mAh or more 3S LiFePO4 if I recall correctly, this is far over sized and needless wight in my opinion. As mentioned in the [operation guide](./OPERATION.md#batteries-and-power), a _fully charged_ 1000&nbsp;mAh 3S LiFePO4 battery is sufficient to run any of the vision systems for around an hour which will suffice for a heat.

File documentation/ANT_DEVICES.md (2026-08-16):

# Working with ANT+ Devices

The ANT+ protocol is used for providing some data from biometric device: the power pedals and heart rate monitors. It's largely being phased out for BLE but we'll stay comfortably in the past.

## Setup

To properly perform the operations needed to use ANT devices you will need some ANT capable receiver and one of their development tools. This can take the form of either:

- ANT USB stick connected to a Windows PC runing [Simulant](https://www.thisisant.com/resources/simulant-1). _You will need to make a free account on their site._
- An Android phone with the [ANT Plugin Sampler App](https://play.google.com/store/apps/details?id=com.dsi.ant.antplus.pluginsampler&hl=en) installed. _This will likely require an old Android phone since many have started dropping ANT support in favour of BLE._

## Recording Expected USB Dongle

The TITAN vision system performs a check on boot to see if an ANT receiver stick is present to determine if it is the primary/front system (ANT present) or not. It does this by checking all the connected USB devices for a vendor and product number (VID/PID) to match what it expects.

>[!IMPORTANT]
> The expected USB dongle must be correctly identified or else no ANT data will be collected for the rider overlays.

This "magic" value it is looking for is recorded in hexadecimal (with lowercase letters) as `ANTStickID` in `titan_startup.py` under `vision/`. An example value is `0fcf:1008` for the currently expected USB stick.

To get the VID/PID of an ANT receiver the [methods differ based on system](https://superuser.com/a/1106248). In either case start by connecting the ANT receiver to your computer.

### Windows USB ID Gathering

Go to "Device manager", find your device, right click on it, select "Properties", go to "Details" tab, select "Hardware IDs" from the drop-down, and you will find an entry of a form:

```terminal
HID\VID_046D&PID_C05A 
```

which are correspondingly vendor and product IDs, i.e. `046d:c05a`

### Linux / RPi USB ID Gathering

Run the following command from your terminal to see pairs of `VID:PID` near the names of all of the USB devices connected.

```bash
lsusb
```

## Pairing Devices

Each ANT device has three device identifying fields that are needed to ensure one connects to the right device. These are the following which are generally 16-bit integers.

- Device number
- Device type
- Transmission type

To acquire this information from a device, one needs to pair with it while using one of the ANT developer tools and record the values reported. These values then need to be copied as appropriate into the `titanant.py` script used under `vision/`.

>[!NOTE]
> There is no need to pair your ANT device to the receiver. Once their identifying information is recorded in the scripts, they will have the ANT receiver search and pair with the devices automatically whenever the system starts.

## Configuring ANT Devices

In TITAN we only use heart rate monitors and torque sensing bicycle pedal ANT devices. Heart rate monitors require no configuration to work properly once paired with a device.

**Torque sensing pedals require a little bit of configuration to properly work**. If I recall correctly, they only need the pedal crank length to be programmed so they properly measure torque and thus power. This can be acheived through the ANT development software mentioned at the start of this file, I personally found using Simulant on PC the easiest.

>[!TIP]
> Once any device is configured it is wise to reboot it and check if the values they report are reasonable through the ANT development tools.

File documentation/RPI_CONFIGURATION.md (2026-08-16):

# Raspberry Pi Configuration

>[!IMPORTANT]
> This is only applicable if starting from scratch with a clean SD card and not using the archived image of TITAN from 2022.

The hardware we use for TITAN are Raspberry Pi Model 3 computers, any subvariant is acceptable (A, B, B+). The system image we have been using for years is for 16&nbsp;GiB microSD cards.

>[!WARNING]
> Much of what was used is now depreciated or obsolete so be careful when updating the images or downloading libraries.

The version of Raspbian _(yes, Raspbian - not Raspberry Pi OS)_ used is "Full" 64-bit version of 11.4 - "Bullseye". Likely the 2022-04-07 release.

The Raspberry Pis were configured years ago with no proper record other than the console log to work with - copied here as `TITAN.bash_history`. From it I've gathered the following pointers on how it was configured.

Check if the VideoCore library and examples are present in the system at `/opt/vc/`. If not try the following remedies:

- Run this in terminal `sudo apt-get install libraspberrypi0`
- Download the `userland` repository at [this commit](https://github.com/raspberrypi/userland/tree/54fd97ae4066a10b6b02089bc769ceed328737e0), the most recent before the 2022 competition, although likely already on the RPi.

With that sorted run the following commands:

```bash
sudo apt install cmake
sudo ldconfig -n /opt/vc/lib
```

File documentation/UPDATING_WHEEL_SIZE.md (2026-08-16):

# Updating Wheel Size

If there are any changes to the _(effective)_ wheel circumference of TITAN they should be reflected properly in the code to ensure we are still calculating speeds and distances correctly from our wheel encoders.

Unfortunately this system inherits a bit of the sloppy design choices I made in 2022 and maybe even as far back as 2019, one such symptom is that we need to update the wheel raduis in multiple places because for some reason I thought it was best to communicate distance in terms of completed rotations rather than a calculated value. If I were to do it again I would only have it set in the microcontroller and provide distance directly.

Luckily the changes are pretty easy to administer in either system. When performing these updates, they should be done for all boards at a time to ensure none are left with the old value - _even the spares!_

## Updating the Microcontroller

The microcontroller has the value hardcoded as `CIRCUMFERENCE_M` in `update_wheel_status()` in `main.c`, simply set it to properly reflect the active circumference in metres.

It may also be necessay to update the number of spokes on the brake disk in this function if the brakedisk is changed.

```c
inline static void update_wheel_status(volatile struct WheelStatus* status, uint32_t capture_period_count) {
    const float CIRCUMFERENCE_M = 2.136;
    const uint8_t SPOKES = 6; // The number of spokes (counts) per complete wheel rotation

    ...
}
```

Once updated you need to program the microcontroller as described in the [firmware `README.md`](../firmware/README.md#programming-the-boards).

## Updating the Video System

In the overlay system the circumference is defined as a global constant `WHEEL_CIRCUMFERENCE_M` at the top of the `main.c` file

```c
const float WHEEL_CIRCUMFERENCE_M = 2.136;
```

Once changed, the overlay code will need to be recompiled into a new binary for the system as described in the [vision system `README.md`](../vision/README.md#compiling-the-overlay-code).

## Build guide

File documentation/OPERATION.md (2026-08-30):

# Operating TITAN

TITAN was designed and tested to be a pretty simple system to operate by requiring no user input beyond a the input to power on, once assembled correctly. This has been preserved with this update to the system, which aimed to not disrupt any of the established TITAN protocols.

>[!NOTE]
> This document assumes the TITAN 2026 electrical system has already assembled and setup. For instructions on how to assemble and setup the TITAN hardware please refer to the [assembly document](./ASSEMBLY.md).

## Batteries and Power

_The system's life force!_ The batteries TITAN was **designed to use 3S LiFePO4 batteries**, so I recommend they continue to be used. Their working range of voltages are 9.0&nbsp;V to 10.8&nbsp;V with a nominal voltage of 9.9&nbsp;V. All batteries should be charged fully prior to any use of TITAN.

Although designed for 3S LiFePO4 batteries, the input of TITAN 2026 can handle a wide range of voltages and still operate without issue. Despite the labeling of `12V MAX`, the RPi board can tolerate between 5&nbsp;V and 17&nbsp;V on the input and provide the needed power for all systems. The stated 12&nbsp;V limit is imposed by the monitor which depending on how the board is configured may draw power from the regulated 5&nbsp;V rail _(in which case the board's own limits still apply)_ or connected directly to the battery which would mean the battery must satisfy the monitor's power requirements. In the the 2022 system the monitors were all designed to handle 12&nbsp;V at most so I kept that warning on the board should the same monitors continue to be used, **please check the monitors used for their power requirements - twice!**

>[!TIP]
> LiFePO4 chemistry batteries are preferred for TITAN due to their safer nature. Their chemistry has a larger range of environmental conditions where it is stable and less dramatic failure modes should the worst come to happen which affords our riders more time to vacate the vehicle in an emergency.

The exact power draw of TITAN is approximately 10&nbsp;W per RPi vision system, about half that for the analog back up system. As such **a 1000&nbsp;mAh 3S LiFePO4 battery can supply a single vision system an hour of operation**. This is plenty for most of our 20 minute heats - but warrants changes for longer testing sessions.

There is circuitry to allow TITAN RPi HATs to seamlessly and safely switch between battery and USB power when in use, should both sources be connected to the board then the battery is selected for power. It is not recommended to use USB power to power an RPi through the HAT as the USB-C connector is configured to only request around 5&nbsp;W of power - enough to run the sensor system.

## Start Up

With TITAN assembled correctly the process to launch the system is pretty straight forward.

> [!CAUTION]
> Failure to follow the battery connection sequence properly may damage the hardware or hinder system operation.

1. Ensure batteries are fully charged
2. Plug in the batteries following this exact order. Each system should automatically begin booting when their battery is connected
   1. Secondary (rear) system
   2. Primary (front) system
   3. Backup system
3. Press the power button (`PWR_RPi`) on RPi systems to boot them if needed - for example if they were shutdown without battery removal

The backup system should show the video feed immediately when turned on. The RPi systems will take about 30 seconds to put the video on screen, which will be preceded with boot messages and a printing of the system's configuration.

## Shut Down

Whenever power is going to be removed from TITAN the following procedure should be followed. Be it at the end of a run, or to conserve battery when staging before a run.

> [!CAUTION]
> Failure to follow this properly may damage the hardware or risk corrupting the data on the RPis.

1. Hold the power button (`PWR_RPi`) on the HAT for a few seconds until it starts shutting down
2. Wait for the video feed to go off and the RPi to shut down properly
   - The video feed should disappear within seconds after the button is pressed, if not press the button again
   - Repeated presses of the off button will not adversely affect the system
   - If the system doesn't shutdown within a minute you may need to connect a keyboard or simply pull the power risking data loss
   - As the RPi shuts down its status LED will flash ten times at 2&nbsp;Hz before going out, that signals it is safe to remove power
3. If desired, disconnect the batteries. They **MUST** be removed in the reverse order they were installed in:
   1. Backup display
   2. Primary system
   3. Secondary system

If the batteries are left in place after the RPis are shutdown, the RPis can be turned on at the press of the power button (`PWR_RPi`). This is useful to do for staging before a run. There is no required order to follow when turning on RPis in this manner because the power supplies have all stabilized.

## Transferring Data To or From the RPis

My _(Savo's)_ preferred method to transfer data was to remove the RPi's micro SD card _(after a proper shutdown with battery removal!)_ and insert it into my computer and directly copy the data of interest onto the computer that way. The only issue is that you'll likely need a Linux machine to recognize the file system the RPis use. Having the SD card in my computer also made it easy to edit some of the scripts to handle things like new power pedals.

Other options include network access or using the RPis as a normal desktop and a USB drive to ferry the data to another computer.

>[!IMPORTANT]
> To get to the desktop of a TITAN RPi one can _quickly_ tap the RPi's power button (`PWR_RPi`) during operation to stop the vision system so the terminal is made visible.

If the button is not working, one can try to manually enter the following sequence of command blindly into the terminal with a keyboard to shut the vision system down. _Best of luck console cowboy!_

```bash
sudo pkill bike
sudo pkill python
```

>[!TIP]
> Entering `startx` in the terminal will start the graphical interface if desired for easier operation of the RPis. _Brace yourself for a slow computer experience._

### Log Files and Locations

By default the TITAN system records data in two locations, one for the videos and another for the ride data.

> [!NOTE]
> All recorded files are timestamped in their names with the start of the run. However the **RPis do not keep time when they are off, so these times will likely lag behind the true start time**. To minimize this time discrepancy the RPis should be allowed to connect to the internet to synchronize their clocks regularly.

| Data | Location | Format |
| --- | --- | --- |
| Ride data | `/home/pi/Desktop/vision/bikelogs/` | `.csv` |
| Video recordings | `/home/pi/Videos` | `.h264` |

### Video Conversion

To convert from `.h264` recordings to the more commonly accepted `.mp4` one may use the following `ffmpeg` command with the appropriate file names substituted for "video":

```bash
ffmpeg -r 60 -i video.h264 -c:v copy video.mp4
```

>[!NOTE]
> The video recordings are known to have portions where the video seems to skip ahead for split seconds. This is likely due to the recording program getting overwhelmed or some hiccup in the `.mp4` conversion process.
>
> Furthermore, the video and overlay/logging are run as separate process so the videos will lack the overlay the rider's had. Also their starting time stamps will likely differ and need a little effort to align if one tries to reconstruct the overlays later.

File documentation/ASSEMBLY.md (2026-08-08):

# Assembly of TITAN 2026

TITAN was once assembled, now it likely is no longer, so someone's got to put it back together. This will be written assuming TITAN's basically being entirely rebuilt.

## Lists of Parts

>[!NOTE]
> These lists do not account for any spare parts, those are up to your discretion.

There are a fair few parts to TITAN needed for operation that need to be packed listed below. Only one unit is needed of each unless specified otherwise.

- 2 x Raspberry Pis Model 3A+ or 3B+
- 2 x 16 GB micro SD cards (larger is fine but the excess storage will not be utilized)
- 2 x approximately 10" 720p HDMI display, 12&nbsp;V supply
- 2 x Raspberry Pi "Spy" camera
- TITAN 2026 HAT assembled for primary operation
- TITAN 2026 HAT assembled for secondary operation
- HDMI cable, 30&nbsp;cm long (for rear rider)
- GPS antenna with SMA connector on 3&nbsp;m cable
- 2.4 GHz antenna with 3&nbsp;m cable
- ANT+ reciever (USB-A)
- Analog pin hole video camera, 12&nbsp;V supply
- 7" analog input display, 12&nbsp;V supply

The following are needed but will likely be already integrated into TITAN's structure, so they don't need to be "packed".

- 3 x Battery extension leads, battery connector to XT-30F, 1.5&nbsp;m long
- 5.5&nbsp;mm barrel jack to barrel jack cable, 3&nbsp;m long
- 5.5&nbsp;mm barrel jack to XT-30F cable, 3&nbsp;m long
- Rear wheel sensor board with harness soldered on
- Brake disk temperature sensor for front wheel with USB-A connector
- USB-A to USB-A cable, 3&nbsp;m long
- HDMI cable, 3&nbsp;m long (for front rider)
- MH-Z19 CO2 sensor with 3&nbsp;m long cable
- 12&nbsp;V power distribution board
- RCA coax video cable, 3&nbsp;m long

## Setup Procedure

>[!CAUTION]
> **All systems must be entirely unpowered for setup!** Remove any and all batteries. The system was not designed for hot-plugging any component so damage may occur as a result.

This starts with the primary digital vision systems for each rider, then the backup system provided to the primary rider.

>[!TIP]
> These steps may be performed in any order when unpowered. Here they are presented in the order that will likely be the most convenient to perform.

1. Check the radio antennas are mounted to the radio window in the tail
   - nRF24 antenna should be positioned normal to the road
   - GPS antenna doesn't need a specific orientation
2. Check the sensors are installed
   - Front wheel brake temperature sensor in wheel bracket
   - Wheel sensor board in the rear wheel's bracket
   - MH-Z19 sensor between the heads of riders
3. Check that the auxiliary sensor connections are made
   - Front wheel sensor intermediate connector is mated near front yoke (might have been disconnected during maintenance or removal of yoke)
   - Front wheel to rear wheel cable harness connection
   - Camera cable extenders are properly securing the ribbon cables if used
   - Antenna cables are routed to electronics area
4. Image the micro SD cards for each RPi and insert them into the RPis
5. Connect the camera cables to each RPi, ensuring they are installed correctly by being perfectly normal to the board
6. Install the RPi HATs, mounted with threaded plastic spacer ideally
7. Insert the ANT+ receiver into the primary/front rider's RPi
8. Connect the sensor to the primary system's HAT paying attention that the sensors are located correctly
9. Connect the radio antennas to the appropriate connectors for the primary board
10. Connect the monitors to the RPis using HDMI cables for video and provide them power from same RPi's HAT
    - In TITAN there should be wires routed from the electronics area to the front rider's viewing area
    - Even the rear rider may require some extension cables to better position the electronics
11. Connect the RPi HATs with the bridge cable, from `SEC_OUT` on the secondary (rear rider's) HAT to `PRIM_IN` on the primary HAT
12. Connect the backup camera to the backup monitor using an RCA cable
13. Connect the backup camera and screen to the 12&nbsp;V power board

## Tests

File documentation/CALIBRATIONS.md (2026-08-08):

# Calibration Protocols

TITAN uses some sensor systems that need calibration to operate at their best, so this document compiles the calibration procedure for those systems.

## Wheel Encoder

On the wheel board there is a circuit which uses an analog IR reflectometer sensor to capture the passing of brake disk spokes. This sensor's analog output is passed through an analog comparator with a hysteresis circuit to be converted into a clean digital signal for the microcontroller to monitor. This section is largely copied from the board's own [`README.md](../hardware/wheel_2026_rev_a/README.md#tuning-the-encoders-comparator-operation).

To calibrate this circuit there are two potentiometers that need to be set: one for the base threshold the sensor's value is compared to, `THRES`, and then a second to increase the amount of hysteresis, `HYST`. Hysteresis is useful in preventing noise on the analog signal to cause multiple switches of the output fooling the system into thinking the wheel is spinning far faster than it is.

This calibration is best performed with the target wheel fully assembled and faired to best reflect the actual operating conditions, as ambient light does affect the sensor. **The only tool needed is a small flat head screwdriver for the potentiometers.** Although this calibration can be performed without any electrical tools, a multimeter or even oscilloscope will help greatly if available.

## Look Ma, No Electrical Tools

Instead of depending on electrical tools, one can complete the calibration with just the status LED present on the board

1. Connect the target wheel board to an RPi HAT board and supply power to the HAT board to power the sensor board - battery or USB power is fine.
2. _Gently_ turn both potentiometers entirely counterclockwise to reset them.
3. Rotate the wheel so that the IR sensor is entirely clear of any brake disk spokes.
4. Check that the LED is lit up, if not there may be an issue with the board or too much ambient IR which will need different conditions for testing.
5. Rotate the wheel so a spoke is directly in front of the IR sensor.
6. Turn `THRES` clockwise to increase it until the LED turns off, remember this as the "low" mark.
7. Spin the wheel and make sure that the LED is turning off with each passing of a spoke, and then back on again. Gradually increase `THRES` by turning it clockwise until the LED is no longer turning on again when the spoke is gone - this is the "high" mark.
8. Set `THRES` to be halfway between the "low" and "high" mark. Spinning the wheel should have the LED flash again with each spoke pass.
9. Keep spinning the wheel and increasing `HYST` by turning it clockwise.
10. Once the LED is no longer changing state with the wheel's rotation, this it the "high" mark.
11. Set `HYST` to be about halfway from the starting/zero point to the "high" mark.
12. Spin the wheel to ensure that the LED is flashing again.

This should roughly center the threshold correctly and provide a decent level of hysteresis. _It is impossible for the human eye to perceive the true effect of hysteresis with the LED alone, so we're basically just guessing this._ After checking with the LED it is nice to start TITAN properly and check that the speed readings shown seem reasonable and do not jump around wildly to accept the calibration.

## The Future is Now Old Man (Electrical Tools)

With some method of monitoring voltage in the system, either with a voltmeter or oscilloscope the process can be performed with more precision by using the solder pads left on the board along the top edge with a ground reference pad for convenience.

The precise way to do this, no _major_ guesstimations here!

1. Connect the target wheel board to an RPi HAT board and supply power to the HAT board to power the sensor board - battery or USB power is fine.
2. _Gently_ turn both potentiometers entirely counterclockwise to "reset" them.
3. Rotate the wheel so that the IR sensor is entirely clear of any brake disk spokes.
4. Check that the LED is lit up, if not there may be an issue with the board or too much ambient IR which will need different conditions for testing.
5. Read the voltage on the test point labeled `RAW`, this is our ambient level.
6. Rotate the wheel so that there is a spoke directly in front of the IR sensor.
7. Record the voltage on the test point labeled `RAW`, this is our presence level.
8. Gradually turn `THRES` potentiometer until the voltage on the test point labeled `THR` is halfway between the ambient and presence levels. _If the spoke is still in front of the IR sensor at this point, the LED should turn off._
9. Spin the wheel to observe the LED turning on and off as the spoke passes.
10. Keep the wheel spinning and probe `OUT`.
11. Gradually increase `HYST` by turning the potentiometer clockwise until the signal on `OUT` shows a single pulse for each spoke pass rather than a series of pulses during the transition. Then turn `HYST` a sliver more - just not too much so that the `OUT` stops switching
    - If you're also able to probe the other two signals you should be able to see that `THR` is changing between two levels and that `RAW` should be able to cross `THR` only once per spoke passing.
    - `RAW` should continue to a level past `THR` after crossing it, so that even if `THR` didn't move `RAW` would not be causing potential switching with any sensor noise.
    - If the hysteresis gets too large then it might make it hard to catch occasional pulses leading to slower perceived speed.
12. Spin the wheel to ensure that the LED is flashing with each spoke passing.

If done correctly with measurements, especially an oscilloscope, then one can be fairly confident in the result of this calibration. Nonetheless, it is still worthwhile to start up TITAN's video system and see the values shown on the overlay match expectations and don't fluctuate wildly.

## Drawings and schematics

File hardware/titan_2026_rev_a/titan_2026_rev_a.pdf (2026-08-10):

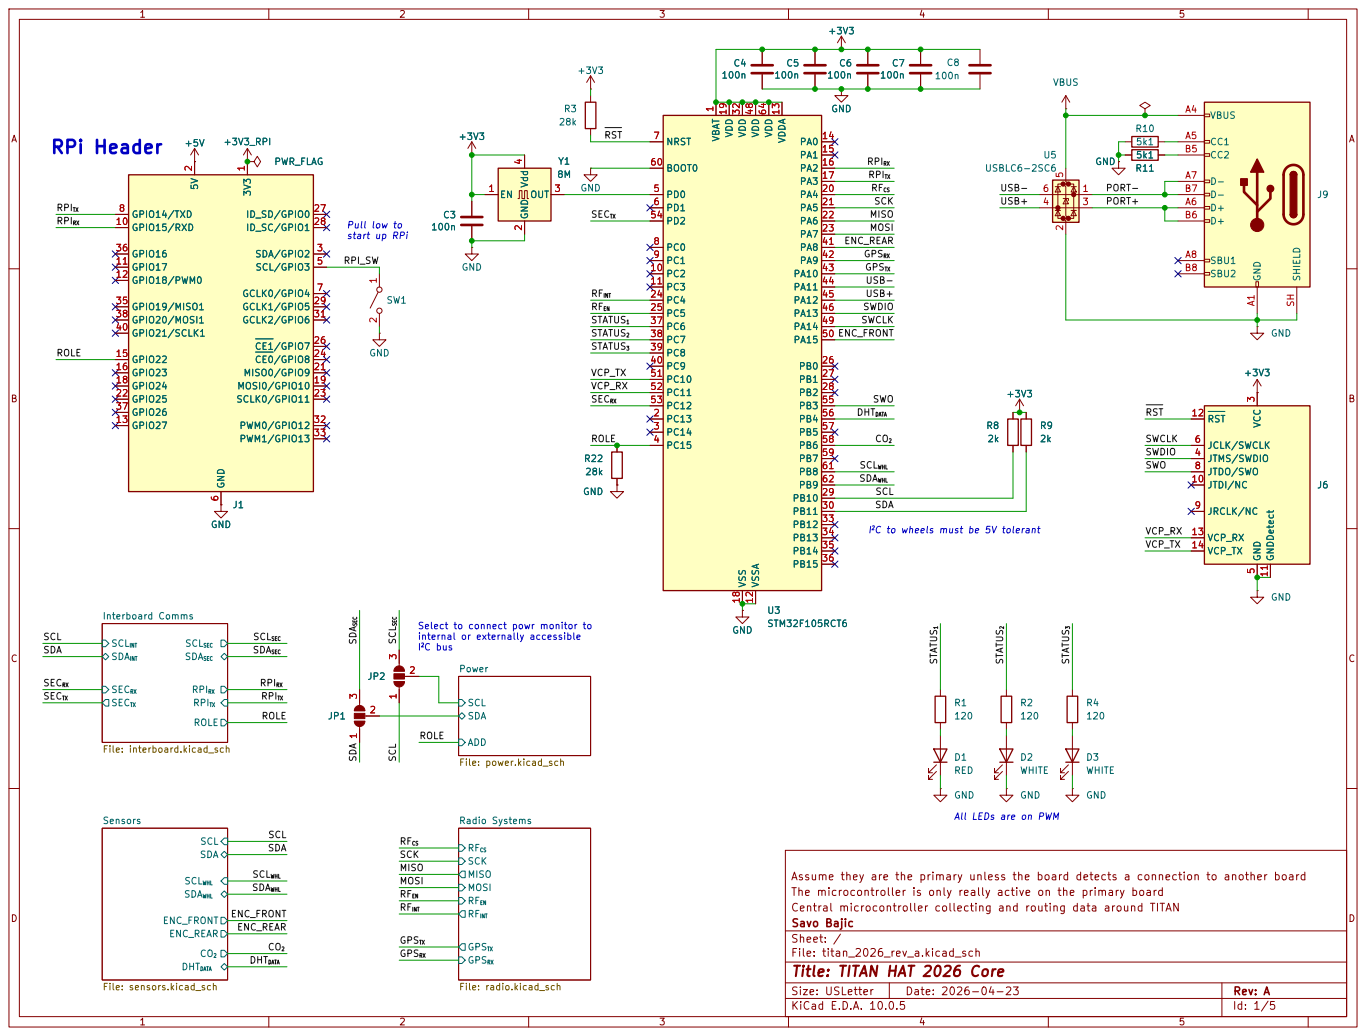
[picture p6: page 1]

I2C to wheels must be 5V tolerant RPi Header

VCP_TX 14 U3
Radio Systems File: radio.kicad_sch SCL SDA

internal or externally accessible

Power File: power.kicad_sch CO2 DHTDATA ENC_FRONT ENC_REAR

SCL SCLWHL SDA SDAWHL Sensors File: sensors.kicad_sch

RFCS RFINT RFEN MOSI MISO

Assume they are the primary unless the board detects a connection to another board
The microcontroller is only really active on the primary board
Central microcontroller collecting and routing data around TITAN
Savo Bajic
Sheet: /
File: titan_2026_rev_a.kicad_sch
Title: TITAN HAT 2026 Core

Size: USLetter | Rev: A
KiCad E.D.A. 10.0.5 | Id: 1/5

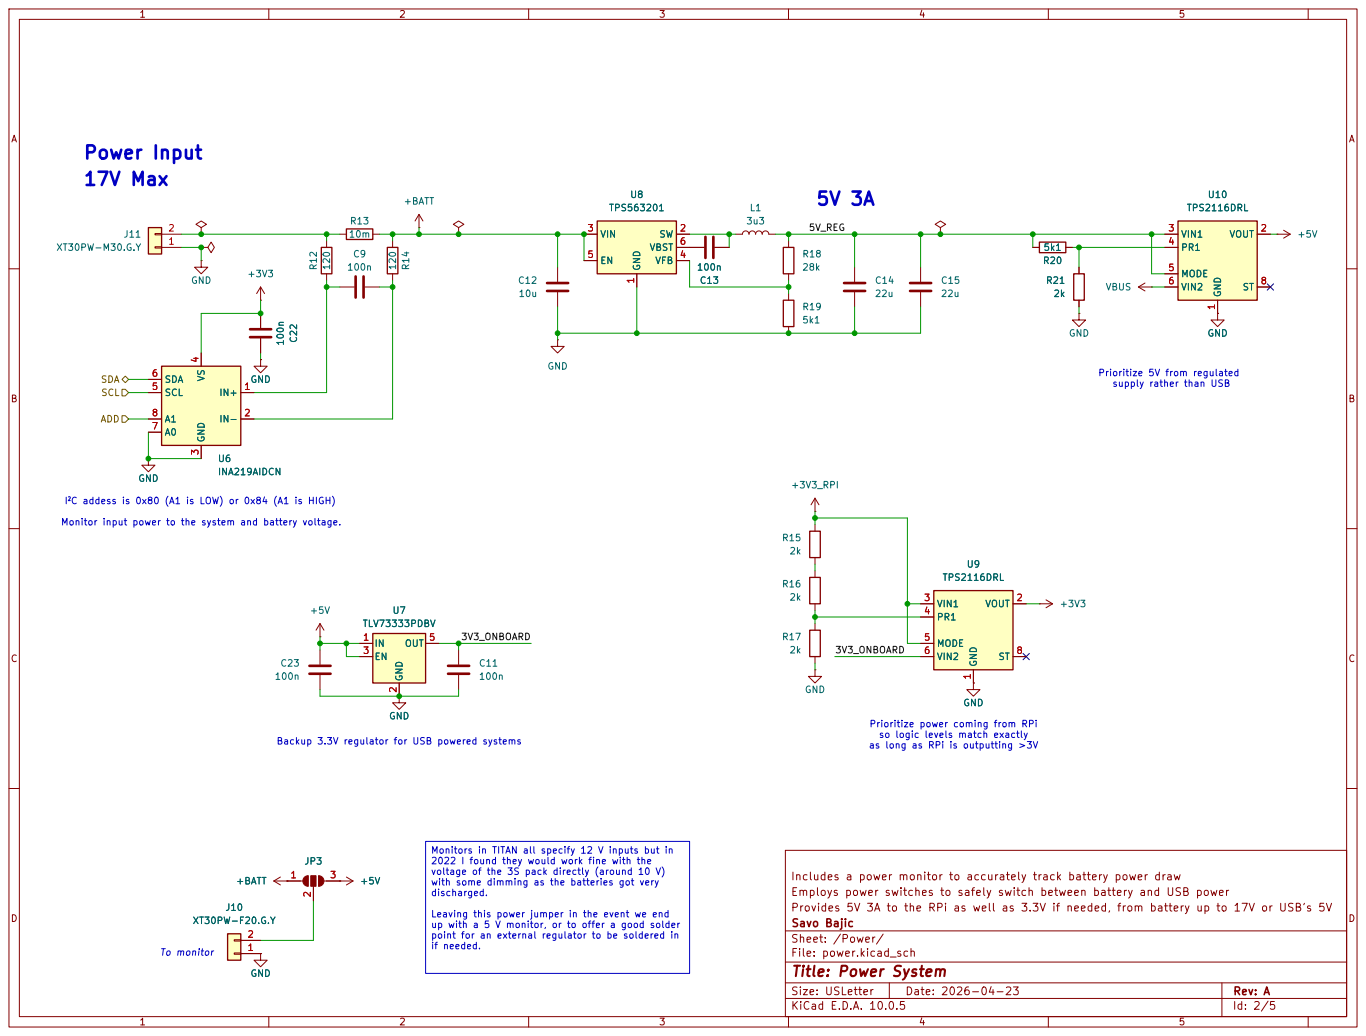
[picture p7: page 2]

Prioritize power coming from RPi so logic levels match exactly as long as RPi is outputting >3V 5V 3A 100n C22 GND U6

supply rather than USB

I2C addess is 0x80 (A1 is LOW) or 0x84 (A1 is HIGH) Monitor input power to the system and battery voltage.

3V3_ONBOARD Monitors in TITAN all specify 12 V inputs but in 2022 I found they would work fine with the

voltage of the 3S pack directly (around 10 V) with some dimming as the batteries got very discharged.

Includes a power monitor to accurately track battery power draw
Employs power switches to safely switch between battery and USB power
Provides 5V 3A to the RPi as well as 3.3V if needed, from battery up to 17V or USB's 5V
Savo Bajic
Sheet: /Power/
File: power.kicad_sch
Title: Power System

Leaving this power jumper in the event we end
up with a 5 V monitor, or to offer a good solder point for an external regulator to be soldered in

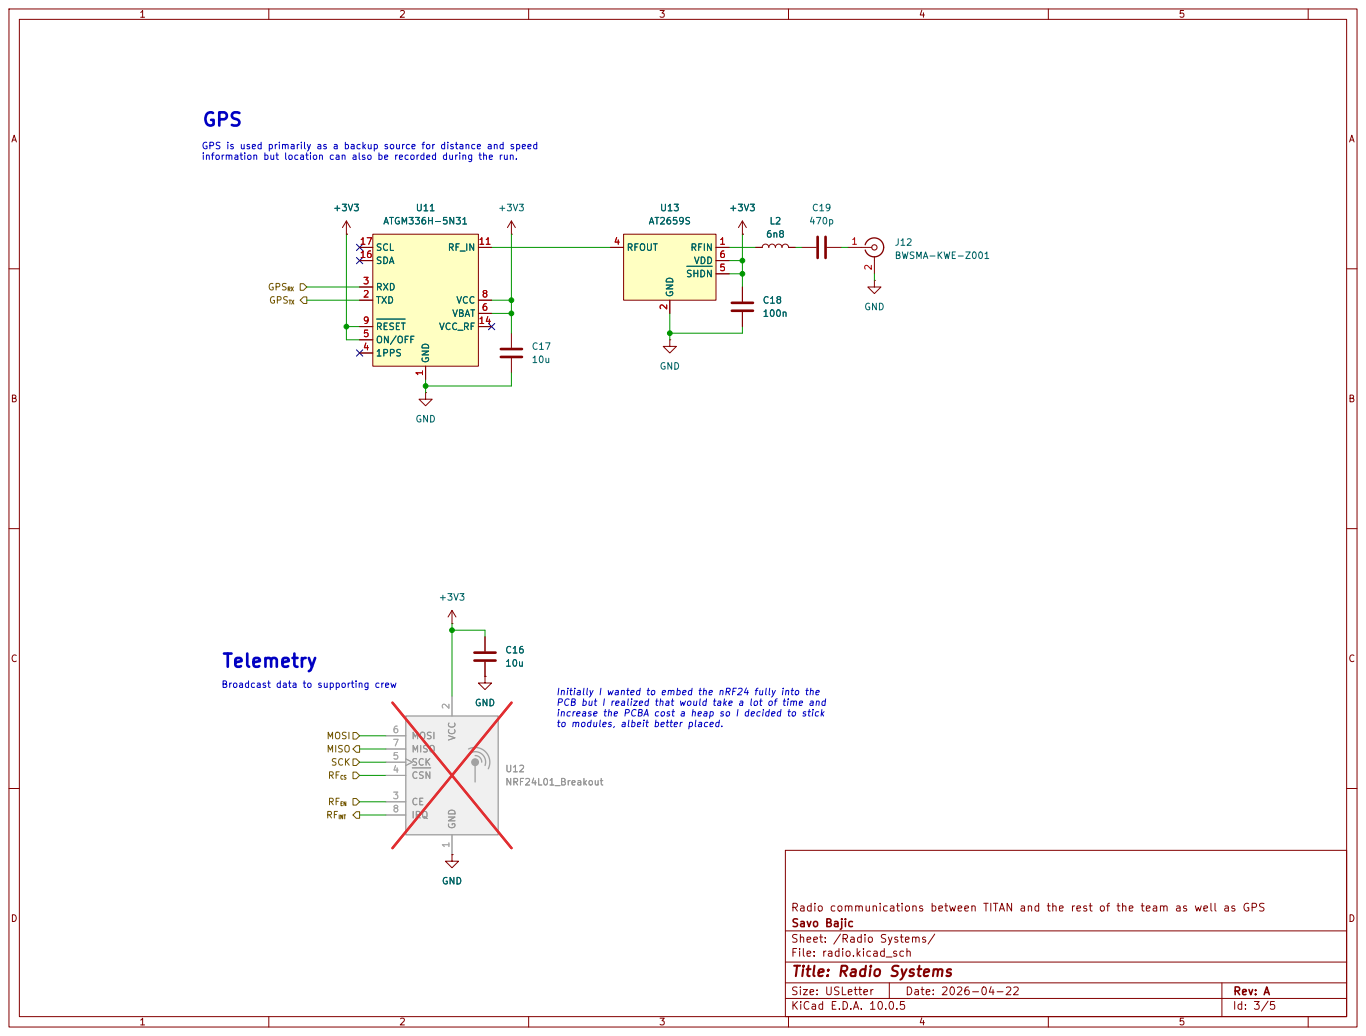
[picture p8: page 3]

information but location can also be recorded during the run. GPS
+3V3 GND
ATGM336H-5N31 GND

GPS is used primarily as a backup source for distance and speed
SDA 16 SCL 17

Broadcast data to supporting crew Telemetry

Initially I wanted to embed the nRF24 fully into the PCB but I realized that would take a lot of time and

increase the PCBA cost a heap so I decided to stick
to modules, albeit better placed.

Radio communications between TITAN and the rest of the team as well as GPS
Savo Bajic
Sheet: /Radio Systems/
File: radio.kicad_sch
Title: Radio Systems

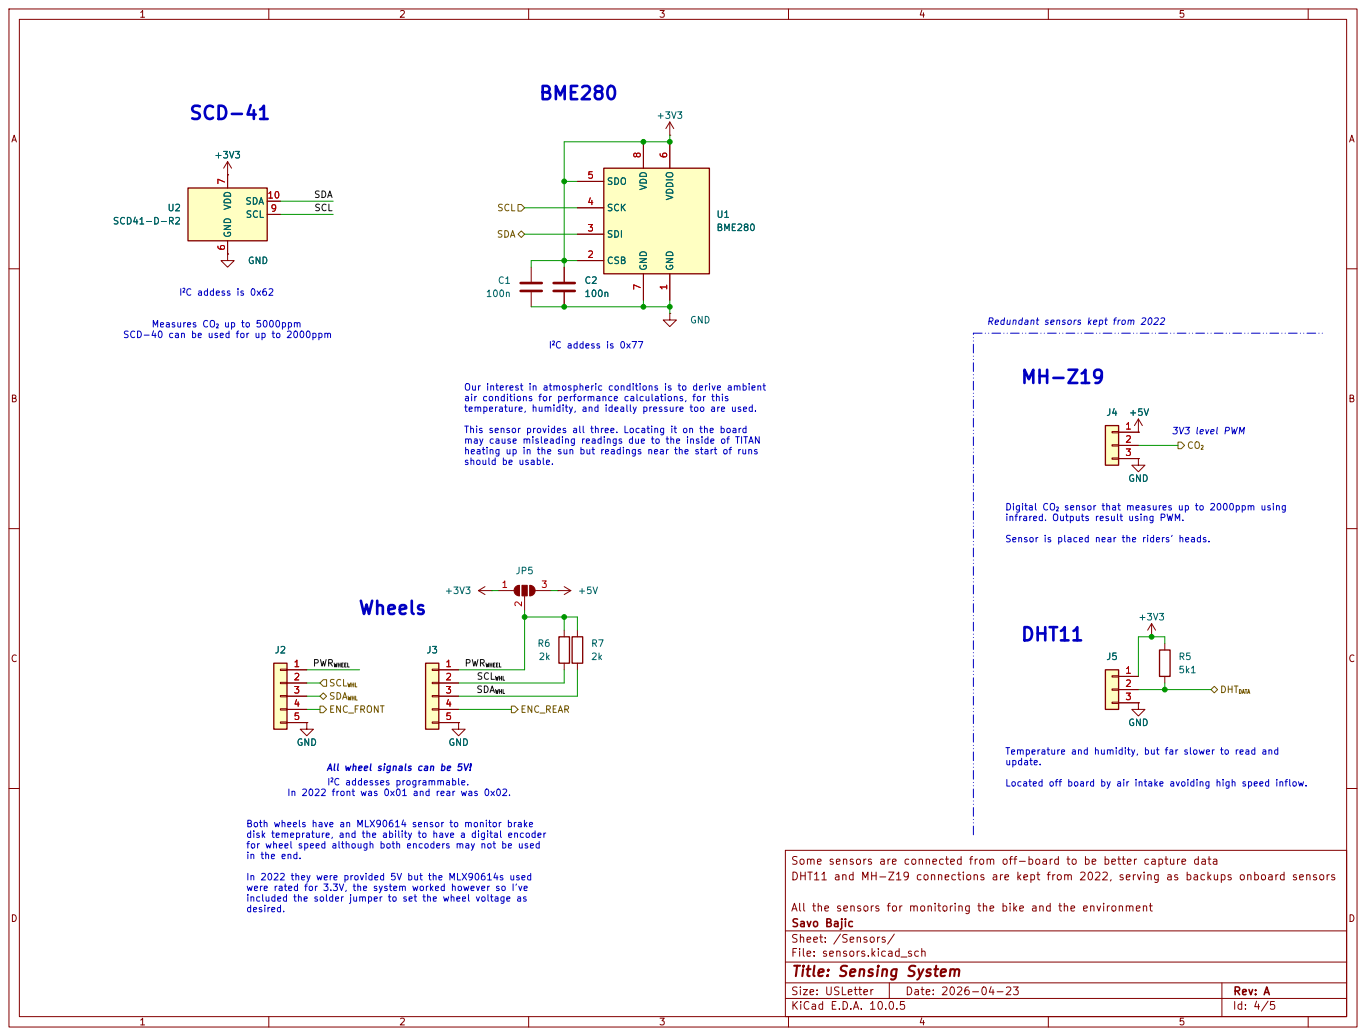
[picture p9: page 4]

Measures CO2 up to 5000ppm
SCD-40 can be used for up to 2000ppm

temperature, humidity, and ideally pressure too are used. This sensor provides all three. Locating it on the board may cause misleading readings due to the inside of TITAN

heating up in the sun but readings near the start of runs

should be usable. Both wheels have an MLX90614 sensor to monitor brake disk temeprature, and the ability to have a digital encoder

update. Located off board by air intake avoiding high speed inflow. Digital CO2 sensor that measures up to 2000ppm using
infrared. Outputs result using PWM. Sensor is placed near the riders' heads.

for wheel speed although both encoders may not be used
in the end.

DHT11 and MH-Z19 connections are kept from 2022, serving as backups onboard sensors Some sensors are connected from off-board to be better capture data

In 2022 they were provided 5V but the MLX90614s used were rated for 3.3V, the system worked however so I've

All the sensors for monitoring the bike and the environment
Savo Bajic
Sheet: /Sensors/
File: sensors.kicad_sch
Title: Sensing System

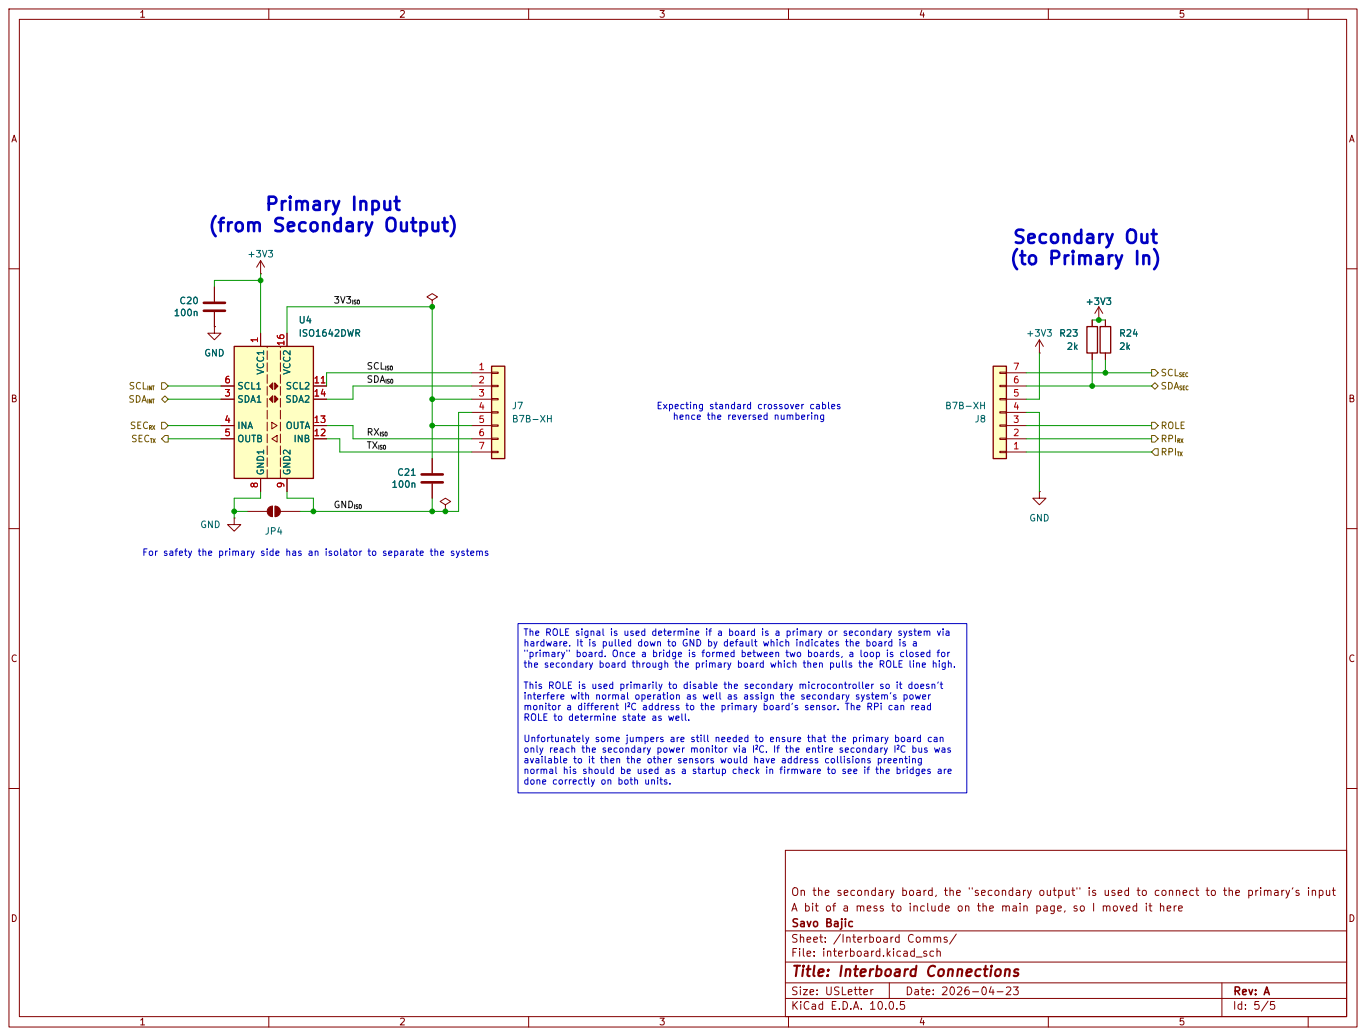
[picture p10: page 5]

normal his should be used as a startup check in firmware to see if the bridges are done correctly on both units. Primary Input (from Secondary Output)

Expecting standard crossover cables hence the reversed numbering

hardware. It is pulled down to GND by default which indicates the board is a
"primary" board. Once a bridge is formed between two boards, a loop is closed for
the secondary board through the primary board which then pulls the ROLE line high. This ROLE is used primarily to disable the secondary microcontroller so it doesn't

interfere with normal operation as well as assign the secondary system's power monitor a different I2C address to the primary board's sensor. The RPi can read ROLE to determine state as well. Unfortunately some jumpers are still needed to ensure that the primary board can

only reach the secondary power monitor via I2C. If the entire secondary I2C bus was available to it then the other sensors would have address collisions preenting
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

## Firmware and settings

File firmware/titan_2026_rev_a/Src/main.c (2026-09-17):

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
/* Includes ------------------------------------------------------------------*/
#include "main.h"
#include "usb_device.h"

/* USER CODE BEGIN Includes */
#include <stdbool.h>
#include "atmosphere.h"
#include "minmea.h"
#include "titan_data.h"
#include "communication.h"
#include "../Drivers/stm32_hal_nrf24_library/NRF24.h"
/* USER CODE END Includes */

I2C_HandleTypeDef hi2c1;
I2C_HandleTypeDef hi2c2;

IWDG_HandleTypeDef hiwdg;

SPI_HandleTypeDef hspi1;

TIM_HandleTypeDef htim1;
TIM_HandleTypeDef htim2;
TIM_HandleTypeDef htim3;
TIM_HandleTypeDef htim4;
TIM_HandleTypeDef htim6;

UART_HandleTypeDef huart4;
UART_HandleTypeDef huart5;
UART_HandleTypeDef huart1;
UART_HandleTypeDef huart2;
DMA_HandleTypeDef hdma_usart1_rx;
DMA_HandleTypeDef hdma_usart2_tx;

/* USER CODE BEGIN PV */
volatile uint16_t mh_z19_co2_ppm = 0;

volatile uint16_t gps_message_length = 0;
volatile uint16_t rpi_message_length = 0;
volatile uint16_t stm_message_length = 0;

const uint32_t I2C_TIMEOUT = 10; // Timeout to be used for I2C interactions

volatile struct TitanSummary summary __attribute__((noinit)); // Preserve data in RAM between boots

// Starting point latitude
const float STARTING_LONGITUDE = -117.043375;
const float STARTING_LATITUDE = 40.393598;

uint8_t rx_addr[5] = {'1', 'N', 'o', 'd', 'e'};
uint8_t tx_addr[5] = {'2', 'N', 'o', 'd', 'e'};

const uint8_t LED_ERROR = 1;
const uint8_t LED_GPS = 2;

const float WHEEL_CIRCUMFERENCE_M = 2.136;
/* USER CODE END PV */

void SystemClock_Config(void);
static void MX_GPIO_Init(void);
static void MX_DMA_Init(void);
static void MX_TIM3_Init(void);
static void MX_I2C1_Init(void);
static void MX_I2C2_Init(void);
static void MX_SPI1_Init(void);
static void MX_TIM4_Init(void);
static void MX_UART4_Init(void);
static void MX_UART5_Init(void);
static void MX_USART1_UART_Init(void);
static void MX_USART2_UART_Init(void);
static void MX_TIM1_Init(void);
static void MX_TIM2_Init(void);
static void MX_IWDG_Init(void);
static void MX_TIM6_Init(void);
/* USER CODE BEGIN PFP */
#ifdef __GNUC__
/* With GCC/RAISONANCE, small printf (option LD Linker->Libraries->Small printf
   set to 'Yes') calls __io_putchar() */
#define PUTCHAR_PROTOTYPE int __io_putchar(int ch)
#else
#define PUTCHAR_PROTOTYPE int fputc(int ch, FILE *f)
#endif /* __GNUC__ */
/* USER CODE END PFP */

/* USER CODE BEGIN 0 */
static HAL_StatusTypeDef led_set_duty(uint8_t led, uint16_t duty) {
	TIM_OC_InitTypeDef sConfigOC = {0};
	sConfigOC.OCMode = TIM_OCMODE_PWM1;
	sConfigOC.Pulse = duty;
	sConfigOC.OCPolarity = TIM_OCPOLARITY_HIGH;
	sConfigOC.OCFastMode = TIM_OCFAST_DISABLE;

	switch (led) {
	case 1:
		return HAL_TIM_PWM_ConfigChannel(&LED_TIMER, &sConfigOC, TIM_CHANNEL_1);
	case 2:
		return HAL_TIM_PWM_ConfigChannel(&LED_TIMER, &sConfigOC, TIM_CHANNEL_2);
	case 3:
		return HAL_TIM_PWM_ConfigChannel(&LED_TIMER, &sConfigOC, TIM_CHANNEL_3);
	default:
		return HAL_ERROR; // Unrecognized LED number
	}

	return HAL_ERROR; // This shouldn't ever be reached
}

static HAL_StatusTypeDef led_sawtooth(uint8_t led) {
	if (led < 1 || led > 3) return HAL_ERROR;

	static uint32_t next_tick[3] = {0, 0, 0};
	static uint32_t current_duty[3] = {0, 0, 0};
	const uint32_t INCREMENT_PERIOD_TICKS[3] = {10, 10, 10};
	const uint16_t MAX_DUTY[3] = {UINT16_MAX / 128, UINT16_MAX, UINT16_MAX};
	const uint16_t DUTY_INCREMENT[3] = {UINT16_MAX / (128 * 500), UINT16_MAX / 200, UINT16_MAX / 200};

	const uint32_t CURRENT_TICK = HAL_GetTick();

	if (CURRENT_TICK < next_tick[led]) return HAL_OK;

	next_tick[led] = CURRENT_TICK + INCREMENT_PERIOD_TICKS[led];

	current_duty[led] = current_duty[led] + DUTY_INCREMENT[led];
	if (current_duty[led] >= MAX_DUTY[led]) current_duty[led] = 0;

	return led_set_duty(led, current_duty[led]);
}
/* USER CODE END 0 */

/**
  * @brief  The application entry point.
  * @retval int
  */
int main(void)
{

  /* USER CODE BEGIN 1 */
	const uint32_t RESET_CODES = RCC->CSR; // Record before they might get cleared
  /* USER CODE END 1 */

  /* MCU Configuration--------------------------------------------------------*/

  /* Reset of all peripherals, Initializes the Flash interface and the Systick. */
  HAL_Init();

  /* Configure the system clock */
  SystemClock_Config();

  /* USER CODE BEGIN SysInit */
  	RCC->CSR = RCC->CSR | RCC_CSR_RMVF; // Clear reset cause for the next run

  	// Check to preserve to ensure data is kept rather than only if it should be cleared since the two may overlap
  	const uint32_t RESETS_TO_PRESERVE_DATA_MASK = RCC_CSR_IWDGRSTF | RCC_CSR_WWDGRSTF | RCC_CSR_SFTRSTF;
  	const bool PRESERVE_DATA = (RESET_CODES & RESETS_TO_PRESERVE_DATA_MASK) != 0;
	if (!PRESERVE_DATA) {
		memset(&summary, 0, sizeof(summary));

    // Non-zero default values
		summary.gps.start_latitude_deg = STARTING_LATITUDE;
		summary.gps.start_longitude_deg = STARTING_LONGITUDE;
	}
  /* USER CODE END SysInit */

  /* Initialize all configured peripherals */
  MX_GPIO_Init();
  MX_DMA_Init();
  MX_TIM3_Init();
  MX_I2C1_Init();
  MX_I2C2_Init();
  MX_SPI1_Init();
  MX_TIM4_Init();
  MX_UART4_Init();
  MX_UART5_Init();
  MX_USART1_UART_Init();
  MX_USART2_UART_Init();
  MX_USB_DEVICE_Init();
  MX_TIM1_Init();
  MX_TIM2_Init();
  MX_IWDG_Init();
  MX_TIM6_Init();
  /* USER CODE BEGIN 2 */
	setbuf(stdin, NULL); //TO HANDLE INPUT BUFFER WHEN USING SCANF/COUT IN C++
	printf("\r\n=========================================\r\n           Starting TITAN 2026\r\n=========================================\r\n");
	if (PRESERVE_DATA) printf("\tData preserved (watchdog reset)\r\n");
	else printf("\tData cleared to defaults\r\n");

	bool non_critical_error = false;
	bool critical_error = false;

	// Start timers once everything's initialized properly
	HAL_TIM_IC_Start_IT(&REAR_ENC_TIMER, TIM_CHANNEL_1);
	HAL_TIM_OC_Start_IT(&REAR_ENC_TIMER, TIM_CHANNEL_2);
	HAL_TIM_IC_Start_IT(&FRONT_ENC_TIMER, TIM_CHANNEL_1);
	HAL_TIM_OC_Start_IT(&FRONT_ENC_TIMER, TIM_CHANNEL_2);
	HAL_TIM_Base_Start_IT(&CO2_TIMER); // Sets up for period elapsed interrupt
	HAL_TIM_IC_Start(&CO2_TIMER, TIM_CHANNEL_1); // Don't care for interrupt on capture here
	HAL_TIM_IC_Start_IT(&CO2_TIMER, TIM_CHANNEL_2);

	HAL_StatusTypeDef ret;
	ret = setup_battery_monitoring(&MAIN_I2C, I2C_TIMEOUT);
	if (ret != HAL_OK) non_critical_error = true;

	ret = atmo_setup(&MAIN_I2C, I2C_TIMEOUT);
	if (ret != HAL_OK) non_critical_error = true;

	ret = setup_brake_disk_sensors(&WHEEL_I2C, I2C_TIMEOUT);
	if (ret != HAL_OK) non_critical_error = true;

	const uint16_t GPS_BUFFER_SIZE = 500;
	char gps_buffer[GPS_BUFFER_SIZE] = {};

	const uint16_t COMMS_BUFFER_SIZE = 64; // Buffer size for data communication buffers
	char rpi_buffer_in[COMMS_BUFFER_SIZE] = {};
	char stm_buffer_in[COMMS_BUFFER_SIZE] = {};
	char rpi_buffer_out[COMMS_BUFFER_SIZE] = {};
	char stm_buffer_out[COMMS_BUFFER_SIZE] = {};

	struct CommunicationInterface primary = { // GPS should never send so don't bother much with it
			.name = "primary",
			.buffer_in = rpi_buffer_in,
			.buffer_in_length = COMMS_BUFFER_SIZE,
			.available_bytes_to_read = &rpi_message_length,
			.buffer_out = rpi_buffer_out,
			.buffer_out_length = COMMS_BUFFER_SIZE,
			.type = INTERFACE_UART_TITAN,
			.prime_read_function = HAL_UARTEx_ReceiveToIdle_IT,
			.send_function = HAL_UART_Transmit_DMA,
			.uart = &PRIM_UART
	};

	struct CommunicationInterface secondary = { // GPS should never send so don't bother much with it
			.name = "secondary",
			.buffer_in = stm_buffer_in,
			.buffer_in_length = COMMS_BUFFER_SIZE,
			.available_bytes_to_read = &stm_message_length,
			.buffer_out = stm_buffer_out,
			.buffer_out_length = COMMS_BUFFER_SIZE,
			.type = INTERFACE_UART_TITAN,
			.prime_read_function = HAL_UARTEx_ReceiveToIdle_IT,
			.send_function = HAL_UART_Transmit_IT,
			.uart = &SEC_UART
	};

	while (GPS_UART.RxState != HAL_UART_STATE_READY) {
		// Wait until ready to receive
	}
	HAL_UART_Receive_DMA(&GPS_UART, (uint8_t*) gps_buffer, GPS_BUFFER_SIZE);

	ret = setup_interface(&primary);
	if (ret != HAL_OK) critical_error = true;
	ret = setup_interface(&secondary);
	if (ret != HAL_OK) critical_error = true;

	struct NRFConfig radio_ext = {
			.hspiX = &RADIO_SPI,
			.spi_w_timeout = 1000,
			.spi_r_timeout = 1000,
			.spi_rw_timeout = 1000,

			.csn_gpio_port = RF_CS_GPIO_Port,
			.csn_gpio_pin = RF_CS_Pin,

			.ce_gpio_port = RF_EN_GPIO_Port,
			.ce_gpio_pin = RF_EN_Pin,
	};

	// Configure radio for dynamic length payloads, although most will be the same length
	ret = nrf24_init(radio_ext, &MICROS_TIMER);
	const bool RADIO_PRESENT = ret == HAL_OK;
	if (RADIO_PRESENT) {
		nrf24_open_tx_pipe(radio_ext, tx_addr);
		nrf24_dpl(radio_ext, enable);
		nrf24_set_rx_dpl(radio_ext, 0, enable);

		nrf24_stop_listen(radio_ext);
		ce_high(radio_ext);
		printf("nRF24 detected and configured to broadcast\n\r");
	}
	else {
		printf("nRF24 not detected, broadcasting will be disabled\n\r");
		// non_critical_error = true; // Radio not installed on any boards used for TITAN so ignore issues
	}

	if (critical_error) {
		Error_Handler();
	}
  /* USER CODE END 2 */

  /* Infinite loop */
  /* USER CODE BEGIN WHILE */
	while (1) {
#ifdef DEBUG
		uint32_t start_loop = MICROS_TIMER.Instance->CNT;
#endif
		HAL_IWDG_Refresh(&hiwdg);

		if (non_critical_error) {
//			led_set_duty(ERROR_LED, UINT16_MAX / 128); // Dim red if systems are diminished but functioning
			led_sawtooth(LED_ERROR); // Cycle error LED slowly
		}
		else led_set_duty(LED_ERROR, 0);
    /* USER CODE END WHILE */

    /* USER CODE BEGIN 3 */
		ret = atmo_conditions_update((struct TitanSummary*) &summary, (uint16_t) mh_z19_co2_ppm);
		ret = read_battery_level((int8_t*)&summary.primary_battery_soc, (int8_t*)&summary.secondary_battery_soc);
		ret = operate_brake_disk_sensors(&summary.front_wheel.brake_disk_temperature_c, &summary.rear_wheel.brake_disk_temperature_c);

		summarize_wheel_data(&summary);

		// Check status of GPS input buffer, takes up to 400 us in Release
#ifdef DEBUG
		uint32_t start = MICROS_TIMER.Instance->CNT;
#endif
		uint_fast16_t current_gps_writing_index = GPS_BUFFER_SIZE - __HAL_DMA_GET_COUNTER(GPS_UART.hdmarx);
		uint_fast16_t last_gps_written_index = (current_gps_writing_index == 0) ? GPS_BUFFER_SIZE - 1 : current_gps_writing_index - 1;
		static uint16_t gps_message_start_index = 0;
		if (gps_buffer[last_gps_written_index] == '\n') {
			bool processed_ok = false;

			if (gps_message_start_index < last_gps_written_index) {
				processed_ok = minmea_process_buffer(&gps_buffer[gps_message_start_index], last_gps_written_index - gps_message_start_index, &summary.gps);
			}
			else {
				// Handle the roll over by copying to a temporary buffer
				char temp_gps[GPS_BUFFER_SIZE];
				uint_fast16_t tail_portion = GPS_BUFFER_SIZE - gps_message_start_index; // In an array of 10 if we start at 6 and need to go to index 2, there are 4 in the tail, 3 in the start
				uint_fast16_t gps_message_length = tail_portion + last_gps_written_index + 1; // +1 to account for zeroth index

				memcpy(temp_gps, &gps_buffer[gps_message_start_index], tail_portion);
				memcpy(&temp_gps[tail_portion], gps_buffer, last_gps_written_index);

				processed_ok = minmea_process_buffer(temp_gps, gps_message_length, &summary.gps);
			}
			// Next message will start after newline
			gps_message_start_index = last_gps_written_index + 1;
			if (gps_message_start_index >= GPS_BUFFER_SIZE) gps_message_start_index = 0;

#ifdef DEBUG
			if (summary.gps.valid_position) {
				uint32_t end = MICROS_TIMER.Instance->CNT;
				uint32_t delta = end - start;
				if (end < start) delta = (end + UINT16_MAX) - start; // Handle rollovers

				printf("GPS processing with a lock took about %lu us\n\r", delta);
			}
#endif
		}
		if (summary.gps.valid_position) {
			led_set_duty(LED_GPS, UINT16_MAX);
		}
		else {
			led_sawtooth(LED_GPS);
		}

		ret = operate_interface(&primary, &summary);
		ret = operate_interface(&secondary, &summary);

		static uint32_t next_broadcast_tick = 0;
		const uint32_t BROADCAST_PERIOD_MS = 500;
		const uint32_t CURRENT_TICK = HAL_GetTick();
		if (CURRENT_TICK > next_broadcast_tick && RADIO_PRESENT) {
			uint8_t trigger_message[] = "{"; // Constantly broadcast summary of TITAN
			uint8_t radio_out[32];
			uint16_t radio_out_length;

			enum MessageStatus status = process_message(&summary, trigger_message, 1, radio_out, sizeof(radio_out)/sizeof(radio_out[0]), &radio_out_length);
			if (status == MESSAGE_PARSED_OK_SEND_RESPONSE) {
				uint8_t radio_err = nrf24_transmit(radio_ext, radio_out, radio_out_length);
#ifdef DEBUG
				switch (radio_err) {
					case 0: // OK
						break;
					case 1:
						printf("Failed radio broadcast: too many retransmissions\r\n");
						break;
					default:
						printf("Failed radio broadcast: %d\r\n", radio_err);
						break;
				}
#endif
			}
			next_broadcast_tick = BROADCAST_PERIOD_MS + CURRENT_TICK;
		}

#ifdef DEBUG
		uint32_t end_loop = MICROS_TIMER.Instance->CNT;
		uint32_t delta_loop = end_loop - start_loop;
		if (end_loop < start_loop) delta_loop = (end_loop + UINT16_MAX) - start_loop; // Handle rollovers

		printf("Loop took about %lu us\n\r", delta_loop);
#endif
	}
  /* USER CODE END 3 */
}

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
/* USER CODE BEGIN 4 */
/**
  * @brief  Retargets the C library printf function to the USART.
  * @param  None
  * @retval None
  */
PUTCHAR_PROTOTYPE
{
  /* Place your implementation of fputc here */
  /* e.g. write a character to the USART1 and Loop until the end of transmission */
  HAL_UART_Transmit(&huart4, (uint8_t *)&ch, 1, 0xFFFF);

  return ch;
}

inline static void update_wheel_status(volatile struct WheelStatus* status, uint32_t capture_period_count) {
	// Using #define to compile hardcoded constant
#define SPOKES 13.0 // The number of spokes (counts) per complete wheel rotation
#define US_PER_COUNT 3.0 // The number of microseconds per clock tick

#define COUNT_TO_KM_P_H (3600000.0 * WHEEL_CIRCUMFERENCE_M / (SPOKES * US_PER_COUNT)) // Divide this by period in count to get speed in km/h

	float speed_km_p_h = COUNT_TO_KM_P_H / (float)(capture_period_count);

	status->speed_kmph = speed_km_p_h;

	status->spoke++;
	if (status->spoke >= SPOKES) {
		status->spoke = 0;
		status->rotations++;
	}

#undef SPOKES
#undef US_PER_COUNT
#undef COUNT_TO_KM_P_H
}

inline static uint16_t calculate_co2_ppm(uint32_t duty_count, uint32_t period_count) {
	// Duty should always be smaller than the full period
	if (duty_count > period_count) {
		return -1;
	}
	const float duty = (float)duty_count;
	const float period = (float)period_count;

	// To deal with the 5% tolerance on timing the measurements are all derived from portions

	const float END_PORTION = 2.0 / 1004.0; // The portion of constant dead time for high and low portions
	const float END_TIME = period * END_PORTION;
	const float HIGH_TIME = duty - END_TIME;

	// Check if the pulse captured was too small and mistaken for negative
	if (HIGH_TIME < 0) {
		return -1;
	}

	const float DATA_PERIOD = period * (1 - (2 * END_PORTION)); // Discount the high and low dead time
	const float PORTION = HIGH_TIME / DATA_PERIOD; // The actual data duty/portion discounting the holds at each level

	const float PPM_RANGE = 5000.0; // Range of measurement for the CO2 sensor installed
	return (uint16_t)(PORTION * PPM_RANGE);
}

void HAL_TIM_IC_CaptureCallback (TIM_HandleTypeDef * htim) {
	uint32_t captured_value = HAL_TIM_ReadCapturedValue(htim, TIM_CHANNEL_1); // All our captures need channel 1 value

	/* For wheel speeds we want to ignore the first capture after an overflow since
	 * it will not properly represent speed since we won't know how many timeouts
	 * have elapsed and accidentally give a false high speed
	 *
	 * To that end if speed is 0 we do one update to a miniscule speed so the next
	 * update recognizes a non-zero value.
	 *
	 * We won't bother with a spoke count update on the first post timeout edge
	 * as it might very well be a reversed rotation. Realistically in normal
	 * operation when we care for distance we won't be going slow enough for this
	 * to matter.
	 */

	if (htim->Instance == REAR_ENC_TIMER.Instance) {
		if (summary.rear_wheel.speed_kmph != 0) update_wheel_status(&summary.rear_wheel, captured_value);
		else {
			summary.rear_wheel.speed_kmph = 0.1;
		}
		return;
	}
	if (htim->Instance == FRONT_ENC_TIMER.Instance) {
		if (summary.front_wheel.speed_kmph != 0) update_wheel_status(&summary.front_wheel, captured_value);
		else {
			summary.front_wheel.speed_kmph = 0.1;
		}
		return;
	}

	if (htim->Instance == CO2_TIMER.Instance) {
		// CO2 calculation
		uint32_t duty_period = HAL_TIM_ReadCapturedValue(htim, TIM_CHANNEL_2);
		mh_z19_co2_ppm = calculate_co2_ppm(duty_period, captured_value);
		return;
	}
}

void HAL_TIM_PeriodElapsedCallback (TIM_HandleTypeDef * htim) {
	if (htim->Instance == CO2_TIMER.Instance) {
		mh_z19_co2_ppm = 0;
		return;
	}
}

void HAL_TIM_OC_DelayElapsedCallback (TIM_HandleTypeDef * htim) {
	// On a timeout we've probably stopped
	if (htim->Instance == REAR_ENC_TIMER.Instance) {
		summary.rear_wheel.speed_kmph = 0;
		return;
	}
	if (htim->Instance == FRONT_ENC_TIMER.Instance) {
		summary.front_wheel.speed_kmph = 0;
		return;
	}
}

void HAL_UARTEx_RxEventCallback(UART_HandleTypeDef *huart, uint16_t Size) {
	if (huart == &GPS_UART) gps_message_length = Size;
	if (huart == &PRIM_UART) rpi_message_length = Size;
	if (huart == &SEC_UART) stm_message_length = Size;
	// Leave the trigger for the next DMA until after the buffer parsed or copied elsewhere to prevent the current message being lost
}

void HAL_UART_ErrorCallback(UART_HandleTypeDef *huart) {
	HAL_IWDG_Refresh(&hiwdg); // Allow the lights to flash for a bit before we recover

	uint32_t error_code = huart->ErrorCode;

	if (error_code == HAL_UART_ERROR_ORE) {
		// As per 27.6.1 in reference manual we can clear this error flag by reading SR and then DR
		(void) huart->Instance->SR;
		(void) huart->Instance->DR;
		if (huart->ErrorCode == HAL_UART_ERROR_ORE) {
			if (huart == &GPS_UART) printf("Error OVERRUN on GPS line PERSISTS\r\n");
			if (huart == &PRIM_UART) printf("Error OVERRUN on primary line PERSISTS\r\n");
			if (huart == &SEC_UART) printf("Error OVERRUN on secondary line PERSISTS\r\n");
		}
		else {
			if (huart == &GPS_UART) printf("Error OVERRUN on GPS line CLEARED. Comms may need a few transactions to recover fully.\r\n");
			if (huart == &PRIM_UART) printf("Error OVERRUN on primary line CLEARED. Comms may need a few transactions to recover fully.\r\n");
			if (huart == &SEC_UART) printf("Error OVERRUN on secondary line CLEARED. Comms may need a few transactions to recover fully.\r\n");
			return;
		}
	}
	else {
		if (huart == &GPS_UART) printf("Error %ld on GPS line\r\n", error_code);
		if (huart == &PRIM_UART) printf("Error %ld on primary line\r\n", error_code);
		if (huart == &SEC_UART) printf("Error %ld on secondary line\r\n", error_code);
	}

	Error_Handler();
}
/* USER CODE END 4 */
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


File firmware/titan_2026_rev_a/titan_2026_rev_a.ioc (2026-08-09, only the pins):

Mcu.UserName=STM32F105RCTx
PA10.GPIO_Label=GPS_TX
PA10.Signal=USART1_RX
PA11.Signal=USB_OTG_FS_DM
PA12.Signal=USB_OTG_FS_DP
PA13.Signal=SYS_JTMS-SWDIO
PA14.Signal=SYS_JTCK-SWCLK
PA15.GPIO_Label=ENCODER_FRONT
PA15.Signal=S_TIM2_CH1_ETR
PA2.GPIO_Label=MAIN_RX
PA2.Signal=USART2_TX
PA3.GPIO_Label=MAIN_TX
PA3.Signal=USART2_RX
PA4.GPIO_Label=RF_CS
PA4.Signal=GPIO_Output
PA5.Signal=SPI1_SCK
PA6.Signal=SPI1_MISO
PA7.Signal=SPI1_MOSI
PA8.GPIO_Label=ENCODER_REAR
PA8.Signal=S_TIM1_CH1
PA9.GPIO_Label=GPS_RX
PA9.Signal=USART1_TX
PB10.GPIO_Label=SCL
PB10.Signal=I2C2_SCL
PB11.GPIO_Label=SDA
PB11.Signal=I2C2_SDA
PB3.Signal=SYS_TRACESWO
PB4.GPIO_Label=DHT
PB4.Signal=GPIO_Input
PB6.GPIO_Label=CO2
PB6.Signal=S_TIM4_CH1
PB8.GPIO_Label=WHEEL_SCL
PB8.Signal=I2C1_SCL
PB9.GPIO_Label=WHEEL_SDA
PB9.Signal=I2C1_SDA
PC10.GPIO_Label=DEBUG_TX
PC10.Signal=UART4_TX
PC11.GPIO_Label=DEBUG_RX
PC11.Signal=UART4_RX
PC12.GPIO_Label=SEC_RX
PC12.Signal=UART5_TX
PC15-OSC32_OUT.GPIO_Label=ROLE
PC15-OSC32_OUT.Signal=GPIO_Input
PC4.GPIO_Label=RF_INT
PC4.Signal=GPIO_Input
PC5.GPIO_Label=RF_EN
PC5.Signal=GPIO_Output
PC6.GPIO_Label=LED_STAT1_RED
PC6.Signal=S_TIM3_CH1
PC7.GPIO_Label=LED_STAT2
PC7.Signal=S_TIM3_CH2
PC8.GPIO_Label=LED_STAT3
PC8.Signal=S_TIM3_CH3
PD0-OSC_IN.Signal=RCC_OSC_IN
PD1-OSC_OUT.Signal=RCC_OSC_OUT
PD2.GPIO_Label=SEC_TX
PD2.Signal=UART5_RX

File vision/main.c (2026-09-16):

#include "main.h"
#define VALUE_AVERAGE_FRAMES 50 // Needs to be #define for array sizes

int overlay_frames_to_render = -1; // Number of frames to render for testing (-1 for infinite)

// Serial configuration
bool using_serial_data = false; // Use serial or not
int serial_line_in_use = -1;

bool collecting_ant_data = false; 	   // Use ANT data from USB?
bool logging_enabled = false;   // Logging configuration
bool cameara_enabled = false;    // Camera
bool system_is_front_rider = true;          // Is front or not

int main(int argc, char *argv[]) {
   printf(ANSI_COLOUR_BLUE "\n==================\n! TITAN 2022 HUD !\n==================" ANSI_COLOUR_RESET);
   
   // Start by reading in arguements
   printf("\n\nExpected arguements when called in order: 'setup string' 'number of frames'\n");
   printf("\tSpecify role with 'f' or 'r' (assumed to be front if not specified)\
         \n\tEnable camera with 'c'\n\tEnable logging with 'l'\
         \n\tEnable ANT collection with 'a'\n\tEnable serial coms with 's'\
         \n\n\tFrames as -1 for infinty, otherwise the number wanted.\
         \n\tE.g. 'bike.bin fc 10' sets system for front operation with camera for 10 frames\n");
   
   // Read in configuration using a run through switch based on arguement count
   // Note: arguement 0 is the call to run the program itself e.g. "./bike.bin"
   int characterToRead = 0;
   switch (argc) {
      case 3:
         // Get frame count
         overlay_frames_to_render = atoi(argv[2]);
      case 2:
         // Go through setup string
         do {
            switch (argv[1][characterToRead]) {
               case 'l':
                  logging_enabled = true;
                  break;
               case 's':
                  using_serial_data = true;
                  break;
               case 'a':
                  collecting_ant_data = true;
                  break;
               case 'c':
                  cameara_enabled = true;
                  break;
               case 'r':
                  system_is_front_rider = false;
                  break;
               case 'f':
                  system_is_front_rider = true;
                  break;
            }
         } while (argv[1][characterToRead++] != '\0'); 
         break;
   }
   

   
   // Reguritate configuration
   printf("\nParsed configuration:\n" ANSI_COLOUR_YELLOW);
   if (system_is_front_rider == true) printf("\tRole: FRONT\n");
   else printf("\tRole: REAR\n");
   printf("\tCamera running: %d\n", cameara_enabled);
   printf("\tCollecting ANT data: %d\n", collecting_ant_data);
   printf("\tCommunicate over serial: %d\n", using_serial_data);
   printf("\tLogging: %d\n", logging_enabled);
   if (overlay_frames_to_render > 0) printf("\tNumber of frames: %d\n\n" ANSI_COLOUR_RESET, overlay_frames_to_render);
   else printf("\tNo limit to number of frames.\n\n" ANSI_COLOUR_RESET);
   
   // Local variables
   int cadence_front_r_m = 0, cadence_rear_r_m = 0; 
   int power_front_w = 0, power_rear_w = 0;
   int heart_rate_front_b_m = 0, heart_rate_rear_b_m = 0;
   int ANTData[] = {0,0,0,0,0,0};
   int battery_soc_rear_percent = 0, battery_soc_front_percent = 0;
   float speed_wheel_km_h = 0.0;
   float dist_wheel_km = 0.0, dist_gps_km = 0.0;
   float temperature_c = 0.0;
   float humidity_per = 0.0;
   float performance_percentage_average = 0.0;
   float brake_temp_front_c = 200.0, brake_temp_rear_c = 200.0;
   int co2_ppm = 0;
   float speed_gps_km_h = 0.0;
   
   // Open serial line
   if (using_serial_data) {
      serial_line_in_use = openLine("/dev/serial0");
      
      if (serial_line_in_use != -1) printf(ANSI_COLOUR_GREEN "Successfully opened serial line!\n" ANSI_COLOUR_RESET);
      else {
         printf(ANSI_COLOUR_RED "FAILED TO OPEN SERIAL LINE!\nReverting to non-serial behavior.\n" ANSI_COLOUR_RESET);
         using_serial_data = false;
      }
   }
   else printf(ANSI_COLOUR_RED "NOT USING SERIAL DATA.\n" ANSI_COLOUR_RESET);
   
   // Inform if ANT data is expected, and set up stdin accordingly
   if (collecting_ant_data) {
      printf("Expecting ANT data to be piped in.\n");
      fcntl(0, F_SETFL, O_NONBLOCK); // Set stdin (0) to be non-blocking
   }
   else if (using_serial_data) printf(ANSI_COLOUR_GREEN "Not collecting ANT data locally, requesting ANT data over serial.\n" ANSI_COLOUR_RESET);
   else printf(ANSI_COLOUR_RED "NOT USING ANY ANT DATA. DISPLAYING RANDOM ANT DATA!\n" ANSI_COLOUR_RESET);
   
   // Start logging
   if (logging_enabled) startLogging();
   else printf(ANSI_COLOUR_YELLOW "NOT LOGGING DATA!\n" ANSI_COLOUR_RESET);
   
   // Print camera status
   if (cameara_enabled) printf(ANSI_COLOUR_RESET "Camera will be launched shortly!\n" ANSI_COLOUR_RESET);
   else printf(ANSI_COLOUR_RED "Camera not configured to start.\n" ANSI_COLOUR_RESET);
      
   sleep(3); // Pause to show config before potentially running camera
   
   printf("\n=========================================================\n");
   printf("RUNNING MAIN LOOP");
   printf("\n=========================================================\n\n");
   
   
   // Timing the entire process
   struct timespec tSystemStart,tSystemEnd;
   clock_gettime(CLOCK_MONOTONIC, &tSystemStart); // Get start time
   clock_t titanProcessClock = clock(); // Get start processor time
   
   startOverlay(cameara_enabled);
   
   // Main HUD loop
   int overlay_frames_left_to_render = overlay_frames_to_render;
   do {
      
      // ANT data
      // printf("Grabbing ANT data\n");
      if (collecting_ant_data == true) getANTDataPipedIn(ANTData, serial_line_in_use);      // It is meant to collect data locally
      else if (using_serial_data == false) { 
         // Cant' collect nor request ANT data, use random numbers
         ANTData[0] = 60;
         ANTData[1] = 60;
         ANTData[2] = 120;
         ANTData[3] = 60;
         ANTData[4] = 60;
         ANTData[5] = 120;
      }
      
      // Copy to nicer named variables
      heart_rate_front_b_m = ANTData[0];
      cadence_front_r_m = ANTData[1];
      power_front_w = ANTData[2];
      heart_rate_rear_b_m = ANTData[3];
      cadence_rear_r_m = ANTData[4];
      power_rear_w = ANTData[5];
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

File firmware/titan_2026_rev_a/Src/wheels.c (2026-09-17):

/*
 * wheels.c
 *
 *  Created on: Aug 2, 2026
 *      Author: savo
 */
#include "main.h"
#include <math.h>
#include "titan_data.h"
#include "cmsis_gcc.h" // Needed to disable and enable interrupts
#include <stdlib.h>
#include "mlx90614.h"
#include "stm32f1xx_hal.h"
#include <stdio.h>

// static const float BRAKE_DISK_EMISSIVITY = 0.6; // Should be between 0 and 1.0, 0.6 for stainless steel in 2022
static const float BRAKE_DISK_EMISSIVITY = 0; // Use the value store in the sensor, recommended to avoid needing the system to reboot the sensors

// MLX sensors default to 0x5A (90)
static const uint8_t FRONT_ADDRESS = 0x01;
static const uint8_t REAR_ADDRESS = 0x02;
static struct MLXDevice front_brake;
static struct MLXDevice rear_brake;

static bool rear_active = false;
static bool front_active = false;

HAL_StatusTypeDef setup_brake_disk_sensors(I2C_HandleTypeDef* bus, uint32_t timeout) {
	UNUSED(timeout);

	HAL_StatusTypeDef ret_overall = HAL_OK;

	front_brake.address = FRONT_ADDRESS;
	front_brake.i2c_bus = bus;
	rear_brake.address = REAR_ADDRESS;
	rear_brake.i2c_bus = bus;

	HAL_StatusTypeDef ret = mlx_setup(front_brake, BRAKE_DISK_EMISSIVITY);
	if (ret == HAL_OK) {
		front_active = true;
		printf("Front brake disk setup success at address 0x%02X\n\r", front_brake.address);
	}
	else {
		front_active = false;
		ret_overall = HAL_ERROR;
		printf("Front brake disk setup failed, error code: %d (Address: 0x%02X)\n\r", ret, front_brake.address);
	}

	ret = mlx_setup(rear_brake, BRAKE_DISK_EMISSIVITY);
	if (ret == HAL_OK) {
		rear_active = true;
		printf("Rear brake disk setup success at address 0x%02X\n\r", rear_brake.address);
	}
	else {
		rear_active = false;
		ret_overall = HAL_ERROR;
		printf("Rear brake disk setup failed, error code: %d (Address: 0x%02X)\n\r", ret, rear_brake.address);
	}

	return ret_overall;
}

HAL_StatusTypeDef operate_brake_disk_sensors(float* front_temp_c, float* rear_temp_c) {
	static uint32_t next_tick_mark = 0;

#ifdef DEBUG
	const uint32_t PERIOD_MS = 1000;
#else
	const uint32_t PERIOD_MS = 100;
#endif

	if (HAL_GetTick() < next_tick_mark) return HAL_OK;
	next_tick_mark = HAL_GetTick() + PERIOD_MS;

	HAL_StatusTypeDef ret_overall = HAL_OK;
	HAL_StatusTypeDef ret = HAL_OK;

	if (front_active) {
		ret = mlx_read_object_temperature_deg_c(front_brake, front_temp_c);
		if (ret != HAL_OK) ret_overall = ret;
	}
	else *front_temp_c = 0;

	if (rear_active) {
		ret = mlx_read_object_temperature_deg_c(rear_brake, rear_temp_c);
		if (ret != HAL_OK) ret_overall = ret;
	}
	else *rear_temp_c = 0;

#ifdef DEBUG
	printf("Brake Temp [*C][Error: %d] F|R: %6.2f | %6.2f\n\r", ret_overall, *front_temp_c, *rear_temp_c);
#endif
	return ret_overall;
}

void summarize_wheel_data(volatile struct TitanSummary* summary) {
	// Generally use average, but if delta grows too large then trust larger value since one sensor may be disconnected
	// Since these values are volatile and change frequently they all need to be read quickly and cached for accurate comparison

	__disable_irq();
	int32_t front_rotations = summary->front_wheel.rotations;
	int32_t rear_rotations = summary->rear_wheel.rotations;
	float front_speed = summary->front_wheel.speed_kmph;
	float rear_speed = summary->rear_wheel.speed_kmph;
	__enable_irq();

	const int32_t ROTATION_TOLERANCE = 50;
	int32_t delta_rotations = front_rotations - rear_rotations;
	if (abs(delta_rotations) < ROTATION_TOLERANCE) summary->effective_rotations = (front_rotations + rear_rotations) >> 2; // Shift to speed up division
	else {
		if (front_rotations > rear_rotations) summary->effective_rotations = front_rotations;
		else summary->effective_rotations = rear_rotations;
	}
	summary->effective_distance_m = (int32_t)((float)summary->effective_rotations * WHEEL_CIRCUMFERENCE_M);

	const float SPEED_TOLERANCE_KMPH = 3.0;
	float delta_speed = front_speed - rear_speed;
	if (fabsf(delta_speed) < SPEED_TOLERANCE_KMPH) summary->effective_speed_kmph = (front_speed + rear_speed) / 2.0;
	else {
		if (front_speed > rear_speed) summary->effective_speed_kmph = front_speed;
		else summary->effective_speed_kmph = rear_speed;
	}
}

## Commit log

2026-04-08 Upload of TITAN 2022 base
    [2172034-1--3DModel-STEP-56544.STEP, DC Power Jack 5.5mm x 2.1mm.STEP, TCRT5000.step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]
2026-04-08 Trying to ignroe KiCad history folder
2026-04-09 Brought KiCad projects into KiCad 10.0
    [titan_2026_rev_a.kicad_pcb, titan_2026_rev_a.kicad_sch, wheel_2026_rev_a.kicad_pcb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]
2026-04-23 Completed rev A schematics
    [2172034-1--3DModel-STEP-56544.STEP, DC Power Jack 5.5mm x 2.1mm.STEP, power.kicad_sch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]
2026-04-23 Added ROLE signal and I2C address notes
    [power.kicad_sch, titan_2026_rev_a.kicad_sch]
2026-04-24 Completed schematics for rev A
    [interboard.kicad_sch, power.kicad_sch, radio.kicad_sch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]
2026-04-25 Added jumper for display voltage supply
    [power.kicad_sch]
2026-04-27 Added note for monitor power jumper
    [power.kicad_sch]
2026-04-28 Using a single switch for RPi power on/off
    [titan_2026_rev_a.kicad_sch]
2026-04-28 Added decoupling cap for INA219
    [power.kicad_sch]
2026-04-28 Added solder bridge for connecting grounds
    [interboard.kicad_sch]
2026-04-28 Drafted initial floor plan of rev A
    [titan_2026_rev_a.kicad_pcb]
2026-04-28 Added power flag to isolated GND
    [interboard.kicad_sch]
2026-04-28 Juggled some connections for routing
    [titan_2026_rev_a.kicad_sch]
2026-04-28 Completed initial layout of rev A
    [titan_2026_rev_a.kicad_pcb]
2026-04-28 Added approximate SMA connector 3D model
    [titan_2026_rev_a.kicad_pcb]
2026-04-29 Added more silkscreen annotations
    [titan_2026_rev_a.kicad_pcb]
2026-04-30 Revised wheel sensor board and documentation
    [TCRT5000.step, wheel_2026_rev_a.kicad_pcb, wheel_2026_rev_a.kicad_sch]
2026-05-01 Expanded on IR possible sensor resolutions
2026-05-01 Wheel rev A PCB as ordered
    Added note to use 3.3V power but 5V was endured before without issue.
    [wheel_2026_rev_a.kicad_pcb, wheel_2026_rev_a.kicad_sch]
2026-05-01 Added 3.3V opeeration note
2026-05-01 Fixed some footprints and part details
    [power.kicad_sch]
2026-05-01 Added jumper to select wheel power
    [sensors.kicad_sch]
2026-05-01 HAT Rev. A ready for ordering
    [titan_2026_rev_a.kicad_pcb, titan_2026_rev_a.kicad_sch]

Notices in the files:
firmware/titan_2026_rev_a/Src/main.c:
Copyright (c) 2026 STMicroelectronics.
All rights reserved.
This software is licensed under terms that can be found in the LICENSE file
